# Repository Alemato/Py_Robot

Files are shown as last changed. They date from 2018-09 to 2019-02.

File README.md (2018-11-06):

# Py Robot Project
## Descrizione 
Il Problema "Z" che il rover dovrà risolvere è il seguente:

Cercare e riconoscere un QR code all'interno di un ambiente circoscritto, nel quale il rover naviga in totale sicurezza evitando gli ostacoli tramite i sensori ultrasuoni e la Pi-Camera.
Una volta travto tale QR Code il Rover accendera il led della OpenMV Camera. 

# Specifice Hardware

## Lista dei componenti da aggiungere al Rover 
### Sono i componenti che vorremmo implementare nel progetto.
###### Componenti già in possesso (durante il progetto)
* 1x OpenMV camera 

###### Componenti compranti durante il progetto
* 1x Microswitch con levetta (il linck a seguire sono 10 pz e li useremo tutti) [(acquistato dal gruppo)](https://www.amazon.it/ROSENICE-Pezzi-Interruttore-Levetta-Micro/dp/B01JRORHGE)
* 1x MakerHawk Lidar Laser Range Modulo Modulo a Singolo Punto Micro Range Pixhawk Compatibile con Cavo  [(acquistato dall'Università)](https://www.amazon.it/MakerHawk-Modulo-Singolo-Pixhawk-Compatibile/dp/B0778B15G7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)
* 1x Multistar LiHV ad alta capacità 5200mAh 3S multi-rotore Lipo pack [(acquistato dall'Università)](https://www.amazon.it/Multistar-LiHV-Capacity-5200mAh-Multi-Rotor/dp/B01BJCZ2G4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)
* 1x Set 2 Lipo Voltage Checker (2S - 8S) [(acquistato dall'Università)](https://www.amazon.it/WOSKY-Battery-Indicator-helicopter-quadcopter/dp/B072J71G72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)
* 1x Turnigy Accucel-6 80W 10A Balancer / Charger LiHV Capace [(acquistato dall'Università)](https://hobbyking.com/it_it/turnigy-accucel-6-80w-10a-balancer-charger-lihv-capable.html)
* 1x Turnigy Temperature Sensor for Battery Charger [(acquistato dall'Università)](https://hobbyking.com/it_it/turnigy-temperature-sensor-for-battery-charger.html)
* 1x Turnigy ignifugo LiPoly Bag Batteria (zip) (200x155x95mm) [(acquistato dall'Università)](https://hobbyking.com/it_it/fire-retardant-lipo-battery-bag-220x155x115mm-with-handle.html)
* 1x Sacco 18x22cm ai polimeri di litio ricarica Confezione [(acquistato dall'Università)](https://hobbyking.com/it_it/lithium-polymer-charge-pack-18x22cm-sack.html)
* 1x Foglio Acrilico 500 x 250 X 4 mm [(acquistato dal gruppo)](https://www.amazon.it/Sintetico-Trasparente-Lastra-500x250-spessore/dp/B00HWRE7SK/) 
* 1x Set 4 cavi TX60 [(acquistato dal gruppo)](https://www.amazon.it/gp/product/B07D71VHFG/)
* 1x Set 5 interruttori 16A 250V [(acquistato dal gruppo)](https://www.amazon.it/gp/product/B00WJLF8OQ/)
* 1x PLA BLU ELETTRICO Ø 1,75 MM 750gr Modello  1PLA60507 [(acquistato dal gruppo)](https://www.filoalfa3d.com/it/filo-175mm/8-pla-blu-elettrico-o-175-mm-8050327033504.html)
* 1x Set 20 viti e dadi 4 X 20 mm  [(acquistato dal gruppo)](https://www.leroymerlin.it/catalogo/bullone-testa-bombata-m4-x-20-mm-34445565-p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)
* 1x Set 6 viti e dadi 6 X 50 mm [(acquistato dal gruppo)](https://www.leroymerlin.it/catalogo/bullone-testa-bombata-m6-x-50-mm-34445726-p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)
* 1x Set 20 dadi 6 mm [(acquistato dal gruppo)](https://www.leroymerlin.it/catalogo/dado-autobloccante--m6-35746193-p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)
* 1x Set 30 viti e dadi [(acquistato dal gruppo)](https://www.weldom.fr/weldom/boulon-6-pans-6-8-3x10-acier-zingue-sac-30-1093856.html)

# Specifiche Software

### Specifiche richieste del Professore 
* Cambiare OS da Raspbian a [Ubuntu-Mate 16.04.2](https://ubuntu-mate.org/raspberry-pi)
* Implementare [Ros Kinetic](http://wiki.ros.org/kinetic) come Publish-Subscribe al posto MQTT 
* Implementare IA in Prolog
* Implementare Pi-camera e algoritmo per la rilevazione degli ostacoli
* Implementare voltometro

### Specifiche Aggiuntuve
* Modifica degli sketch degli arduini, standardizzazione in nodi ROS

## Funzione del Microswitch con levetta
Data la scarsa precisone nel rilevare gli ostacoli sottili, ad esempio un piede della sedia, da parte dei tre sensori ad ultrasuoni, i Microswitch con levetta risolveranno tale problema funzionando come un Bumper Sensor.  

## Lista Cartelle e descrizione contenuto

>
py_robot: cartella pricipale che contiene tutto il progetto del rover fisico
>
py_robot_v_rep: cartella che contiene tutto il progetto in versione v-rep
>

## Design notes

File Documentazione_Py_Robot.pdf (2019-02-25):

# DOCUMENTAZIONE PY_ROBOT

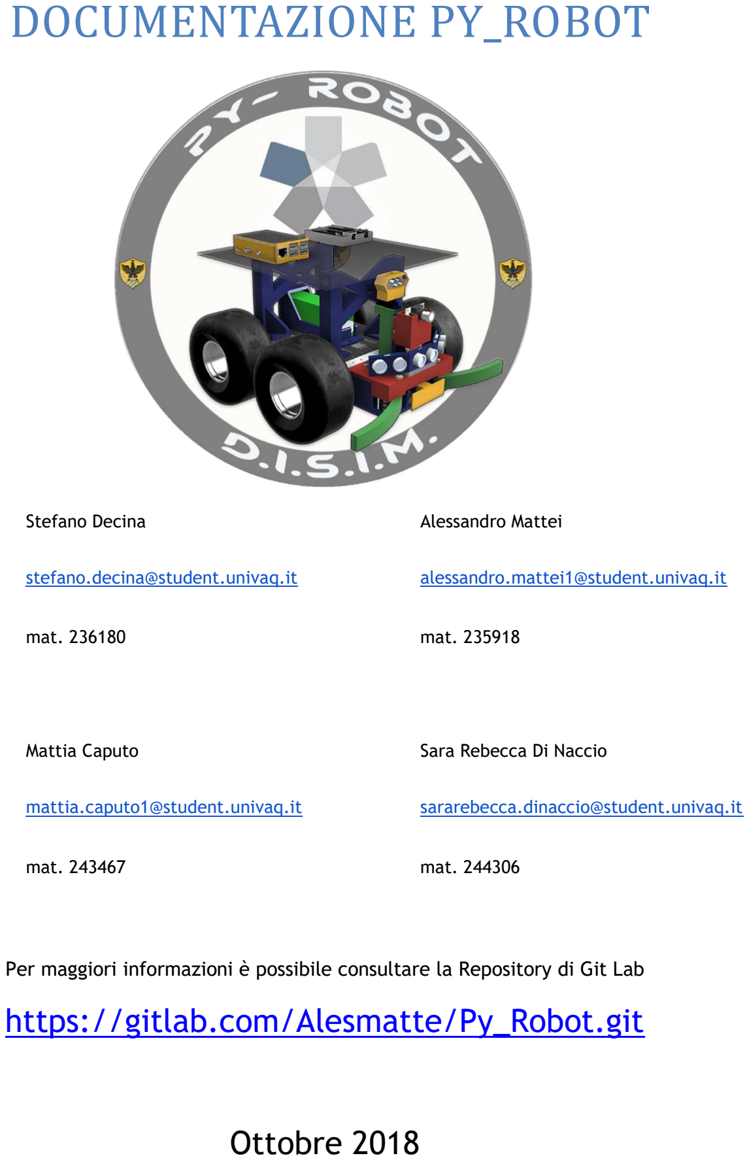
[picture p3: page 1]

Stefano Decina | Alessandro Mattei
stefano.decina@student.univaq.it | alessandro.mattei1@student.univaq.it
mat. 236180 | mat. 235918
Mattia Caputo | Sara Rebecca Di Naccio
mattia.caputo1@student.univaq.it | sararebecca.dinaccio@student.univaq.it
mat. 243467 | mat. 244306

Per maggiori informazioni è possibile consultare la Repository di Git Lab

# https://gitlab.com/Alesmatte/Py_Robot.git

# Ottobre 2018

# SOMMARIO

Sommario | 2
Introduzione | 6
Ruoli dei membri del Team: | 6
Requisiti Funzionali | 7
Componenti del Rover | 7
Telaio del rover | 8
Motori | 8
Ruote | 9
Motor Driver L298N | 10
Pins L298N Motor Driver | 11
Batteria | 13
Sensore Sonar | 16
Pin hc-sr04 | 16
Principio base di funzionamento: | 17
Compass CMP11 | 17
Frequenza di aggiornamento di dati | 18
Selezione della modalità | 18
Comandi Seriali | 19
Calibrazione del CMPS11 | 21
Calibrazione di CMPS11 per funzionamento solo orizontale | 21
Ripristono della calibrazione di fabbrica del CMPS11 | 22
Modifica della velocità di trasmissione | 22
OpenMV Cam M4 V2 | 22
Dimensioni | 23
Pi Camera | 24
Voltometer | 24
Specifiche | 24
Raspberry Pi 3 model B | 25

Accesso alla Raspberry pi 3 | 25
Arduino UNO R3 | 27
Arduino Nano V3.2 | 29
Disegni e Stampe 3D | 30
Baffi | 30
Corpo Frontale | 30
Torri | 31
Case Batteria | 31
Scatola per Alimentazione | 31
Supporto Sonar | 32
Supporto Principale | 32
Connessioni | 33
Arduino Uno – Sonar e Voltmeter | 33
Left Sonar | 33
Right Sonar | 33
Front Sonar | 34
Schema di connessione | 34
Arduino UNO - Compass | 35
Compass | 35
Schema di connessione: | 35
Arduino Nano – Motor Driver e Switch | 36
Motor Driver Sinistro | 36
Motor Driver Destro | 36
Switch 1 | 37
Switch 2 | 37
Switch 3 | 37
Schema di connessione: | 38
Introduzione a ROS | 39
Sistemi operativi Supportati da Ros | 39
ROS Livello file system | 40

ROS Computation Graph Level | 40
Codice | 42
Nodi | 42
Arduino uno: Compass Node | 42
Arduino Nano: Motor Driver & Switch Node | 44
Arduino Nano: Sonar & Voltometer Node | 49
Controller Node | 51
Open_MV Node | 55
Open_CV Node | 57
Prolog_IA_Node | 58
Node Launcher | 65
Messaggi | 65
Compass Node Message | 66
Controller Node Message | 66
Controller To Motor Node Message | 66
MV Camera Node Message | 66
Motor_Switch Node Message | 66
Pi Camera Node Message | 66
Prolog IA Node Message | 67
Sonar_Volt Node Message | 67
Codici VRep | 67
Nodi | 67
Controller Node | 67
Lidar_Compass Node | 72
Motor_Switch Node | 75
OpenCV Node | 79
Prolog_IA Node | 81
Sonar_Volt Node | 90
Launcher | 92
Messaggi | 92

Controller Node Message | 92
Controller to Lidar Node Message | 93
Controller to Motor Node Message | 93
Lidar Compass Node Message | 93
MV Camera Node Message | 93
Motor Switch Node Message | 93
Pi Camera Node Message | 93
Prolog Ia Node Message | 93
Sonar Volt Node Message | 94
Diagrammi | 94
Class Diagram parte fisica | 94
Class Diagram parte virtuale | 95
Component Diagram | 96
Sequence Diagram | 97
NOTE | 98
lIstino prezzi | 100

# CAPITOLO 1

## INTRODUZIONE

Questo Progetto è l’esame finale del corso “Intelligent System and Robotics Laboratory” del Professore Giovanni De Gasperis.

Lo scopo di questo progetto è quello di aggiornare e aggiungere nuove caratteristiche al rover già sviluppato del precedente anno dal team “SmartExploreX”.

In questa nuova versione è stato ridefinito il problema “Z”:

- Navigare liberamente in un ambiente circoscritto, senza urtare oggetti circostanti a lui, in totale sicurezza.
- Cercare e riconoscere un QR code all'interno di un ambiente circoscritto.
- Una volta trovato tale QR Code il Rover emetterà un suono tramite un Buzzer.

## RUOLI DEI MEMBRI DEL TEAM:

### Stefano Decina:

- Sviluppo Arduino
- Sviluppo Ros
- Modellazione 3D per stampe 3D
- Animazione 3D
- Sviluppo V-rep
- Sviluppo I.A.
- Beta tester

### Alessandro Mattei:

- Specialista Hardware
- Implementazione Raspberry
- Sviluppo Arduino
- Sviluppo Ros
- Sviluppo V-rep
- Sviluppo OpenMV
- Sviluppo OpenCV
- Sviluppo I.A
- Beta Tester

### Mattia Caputo:

- Sviluppo V-rep
- Sviluppo Ros
- Sviluppo OpenCV
- Sviluppo I.A.
- Beta tester
- Presentazione

### Sara Rebecca Di Naccio:

- Sviluppo Arduino
- Sviluppo Ros
- Sviluppo I.A
- Documentazione
- Presentazione
- Beta tester

REQUISITI FUNZIONALI

Il rover deve:

- Navigare liberamente e in sicurezza in un ambiente sconosciuto.
- Riconoscere gli ostacoli tramite pi-camera e sempre tramite essa riconoscere il percorso più sicuro.
- Riconoscere gli ostacoli tramite i sensori a ultrasuoni.
- Riconoscere gli ostacoli tramite il LIDAR.
- Riconoscere un urto con un oggetto tramite i micro-switch
- Fermarsi e cercare una via sicura in caso di urto.
- Riconoscere un QR code tramite OpenVM e fermarsi.
- Evitare gli ostacoli presenti nell’ambiente.
- Aggiustare la direzione tramite la bussola.

# COMPONENTI DEL ROVER

Il rover è composto dai seguenti componenti:

- 1X Telaio del rover, in alluminio.
- 4X Motori spazzolati da 12V 0,37A.
- 4X Ruote da offroad.
- 2X Motor Driver L298N.
- 1X Batteria LiHV 3S 5200mah 10C con uscita 52A (in sostituzione alla batteria li-ion 12v 4500mah con uscita 2A, non in grado di alimentare tutto il sistema).
- 3X Sensori ad ultrasuoni HC-SR04 (due in più rispetto alla versione precedente del rover).
- 1X Micro servo SG90 (non presente nella versione precedente del rover).
- | 1X Analog | voltage divider V2 (Non presente nella versione precedente del rover)
- 1X Compass CMP11 Tilt Compensated Magnetic Compass.
- 1X OpenMv (non presente nella versione precedente del rover).
- 1X Pi-Camera (non presente nella versione precedente del rover).
- 1X Raspberry Pi 3 model B
- 1X Arduino Uno R3
- 2X Arduino Nano V3.2
- 10X Micro Switch a levetta (non presenti nella versione precedente del rover).
- 1X Plexiglass di dimensioni:
- Vari Componenti disegnati e stampati in 3D

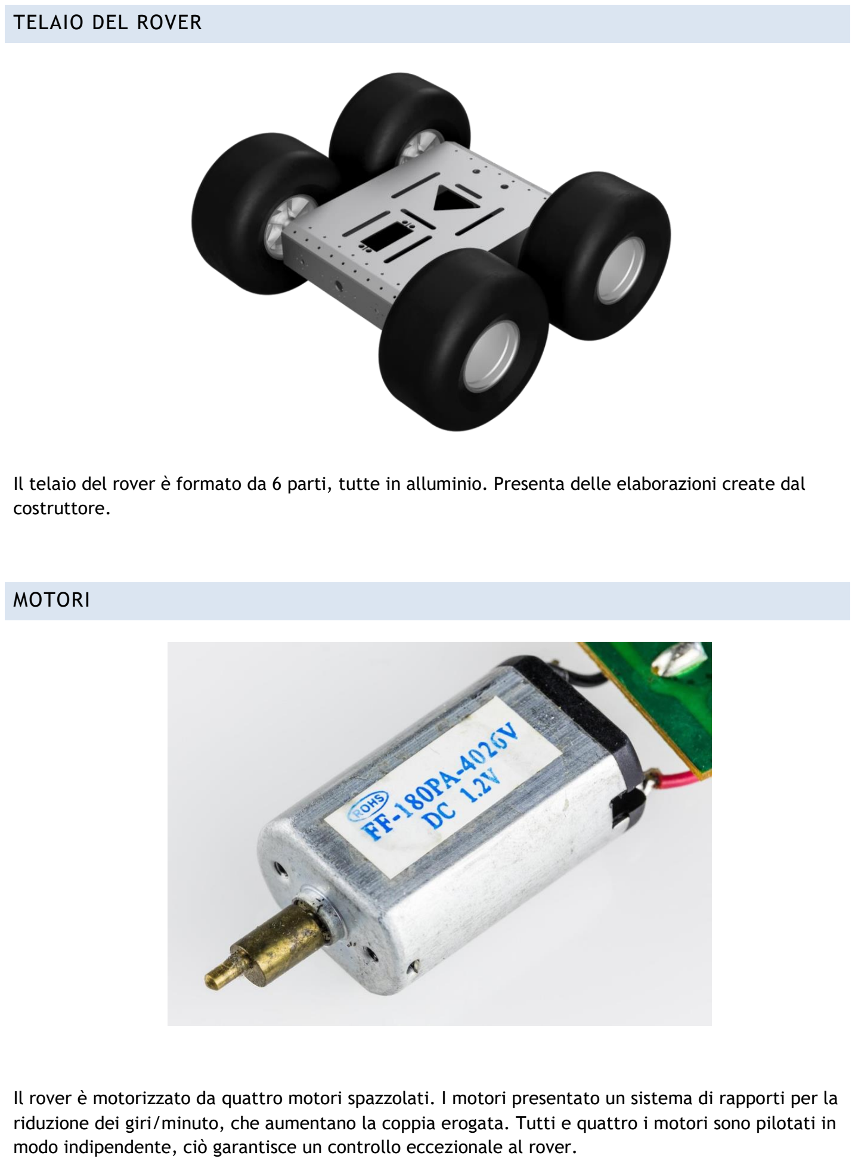
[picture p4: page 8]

TELAIO DEL ROVER

Il telaio del rover è formato da 6 parti, tutte in alluminio. Presenta delle elaborazioni create dal costruttore.

MOTORI

Il rover è motorizzato da quattro motori spazzolati. I motori presentato un sistema di rapporti per la riduzione dei giri/minuto, che aumentano la coppia erogata. Tutti e quattro i motori sono pilotati in modo indipendente, ciò garantisce un controllo eccezionale al rover.

## Specifiche tecniche:

Tipologia di motore: | Spazzolato con riduzione
Tipologia di corrente di funzionamento: | DC
Voltaggio Nominale: | 12V
Amperaggio Nominale: | 0.37A
Rapporto di riduzione: | ND

RUOTE

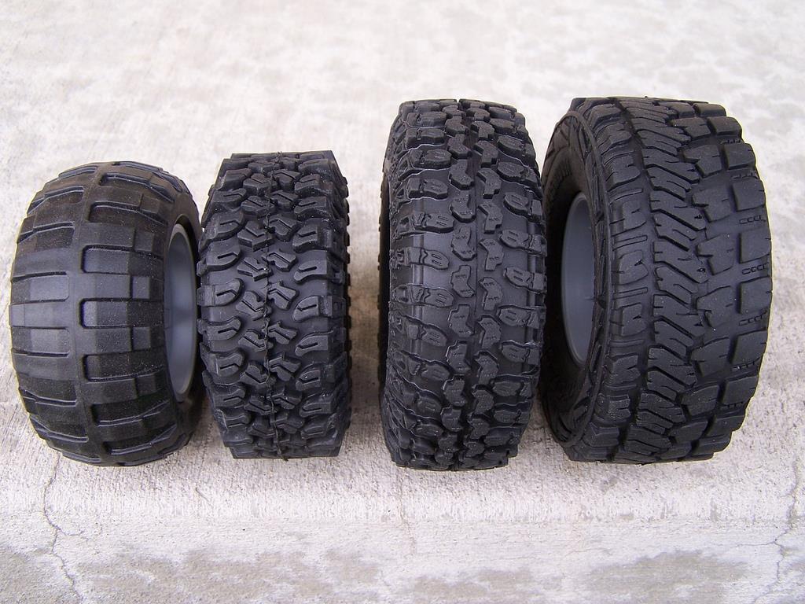
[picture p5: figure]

Il rover è dotato di quattro ruote di tipo off road.

## Specifiche tecniche:

Dimensioni: | ND

MOTOR DRIVER L298N

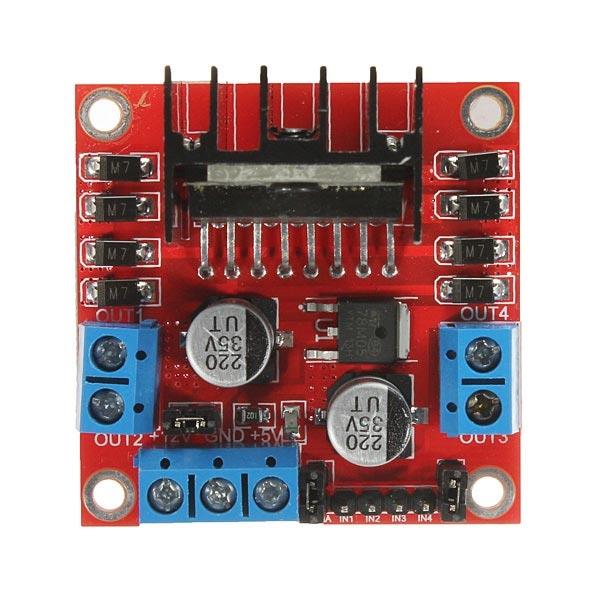
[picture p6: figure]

Il rover è dotato di 2 motor driver L298N.

La funzione dei motor driver è quella di prendere un segnale di controllo a bassa corrente e trasformarlo in un segnale a più alta potenza in grado di pilotare un motore. In questo progetto ne useremo 2 perché ciascun driver può pilotare autonomamente 2 motori.

Un H-Bridge è un circuito in grado di pilotare una corrente in entrambe le polarità ed essere controllato dalla Pulse Width Modulation (PWM). Una modulazione a larghezza di impulso (PWM) è una tecnica di modulazione utilizzata per codificare un messaggio in un segnale pulsante. Sebbene questa tecnica di modulazione possa essere utilizzata per codificare le informazioni per la trasmissione, il suo uso principale è quello di consentire il controllo della potenza fornita ai dispositivi elettrici, in particolare ai carichi inerziali come i motori. Più gli impulsi sono lunghi più la ruota si gira più velocemente, più gli impulsi sono brevi, più lentamente ruota la ruota idraulica. I motori dureranno molto più a lungo e saranno più affidabili se controllati tramite PWM

## Specifiche tecniche:

- | Tensione di alimentazione: | VM = 35V (max.)
- | Corrente di uscita Iout: | 2 A (picco)
- | Modalità di funzionamento: | CW / CCW / freno corto / arresto

PINS L298N MOTOR DRIVER

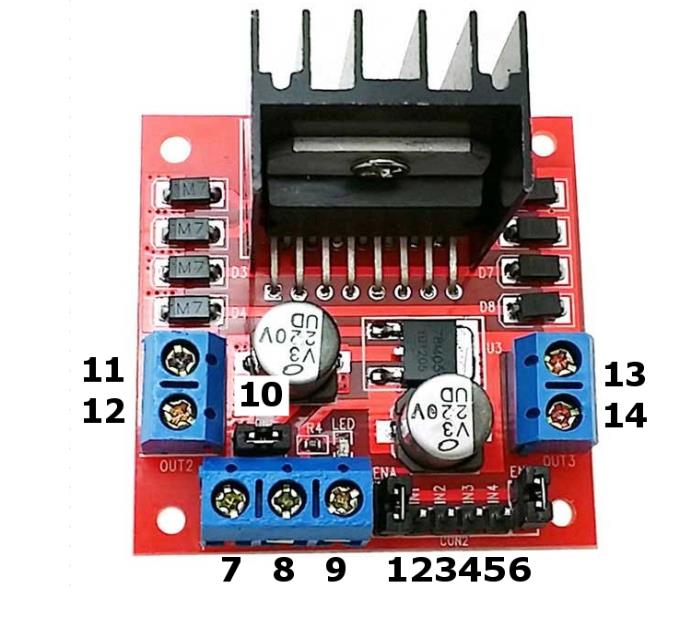
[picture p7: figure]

N° | DESCRIZIONE
1 | ENA - ponticello di abilitazione motore a corrente continua A Non rimuovere nel caso si utilizzi un motore passo-passo. Connettersi a un'uscita PWM per il controllo della velocità del motore DC.
2 | IN 1
3 | IN 2
4 | IN 3
5 | IN 4
6 | ENB - ponticello di abilitazione motore a corrente continua B Non rimuovere nel caso si utilizzi un motore passo-passo. Connettersi a un'uscita PWM per il controllo della velocità del motore DC.

7 | Collegare la tensione di alimentazione del motore, massima di 35V DC. Rimuovere il ponticello [10] se la tensione è > 12V DC
8 | GND
9 | uscita 5V se 12V ponticello in luogo, ideale per alimentare il vostro Arduino (etc)
10 | jumper 12V - rimuovere questo se si utilizza una tensione di alimentazione superiore a 12V DC. Ciò consente l'alimentazione tramite il regolatore 5V di bordo
11 | DC motor 1 "+" o motore passo-passo A +
12 | motore DC 1 "-" o motore passo-passo A-
13 | motore a corrente continua 2 "+" o motore passo-passo B +
14 | motore DC 2 "-" o motore passo-passo B-

BATTERIA

Il rover nella precedente versione era dotato di una batteria Li-ion con uscita di 1A che non era in grado di alimentare tutto il sistema, abbiamo quindi dovuto sostituire la batteria con una più potente una Lipoly LiHV.

Le batterie Lipoly ad alta tensione (LiHV) offrono una maggiore densità di potenza rispetto alle tradizionali batterie lipo che consentono di aumentare i tempi di utilizzo senza la penalità di peso aggiuntivo.

LiHV sta per "High Voltage Lithium Polymer”. I vantaggi delle batterie LiHV sono la maggiore potenza e tempi di funzionamento più lunghi. Le batterie LiHV possono essere caricate a 4,35 V per cella, superiori alle normali batterie LiPo che si trovano a 4,20 V. Ad esempio, un pacco LiHV 3S caricato a 4,35 V darebbe 13,05 V. Considerando che una batteria Lipo con la stessa carica otterrebbe solo 12,6V. Le batterie LiHV hanno anche una resistenza interna inferiore.

Il grosso svantaggio risiede nella pericolosità delle batterie stesse.

La batteria può esplodere se corto-circuitata, a causa della bassissima resistenza interna e della conseguente tremenda corrente impulsiva che attraversa la cella. Inoltre, una cella Li-Poly può incendiarsi facilmente se forata, per cui le batterie sono, in varie applicazioni, ricoperte da un involucro plastico che dovrebbe prevenire le forature.

Queste batterie necessitano di usare caricabatterie specifici (vedi foto), per evitare, appunto, incendi ed esplosioni.

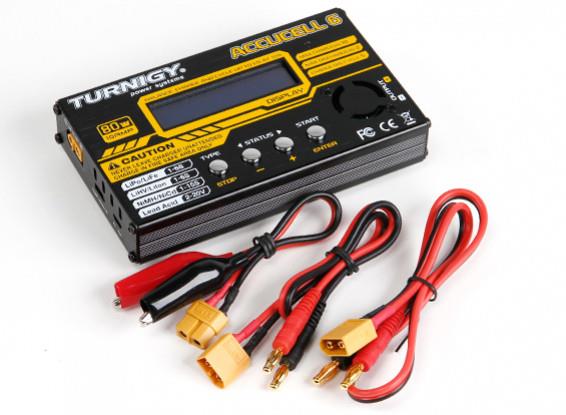
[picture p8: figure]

## Specifiche tecniche Batteria:

Capacità Minima: | 5200mAh
Configurazione: | 3S / 11.4v / 3Cell

Costante di Scaricamento Nominale: | 10C
Constante di Scaricamento Picco (10sec): | 20C
Peso Batteria: | 318g
Dimensioni: | 108 x 36 x 47 mm
Charge Plug: | JST-XH
Discharge Plug: | XT60

SENSORE SONAR

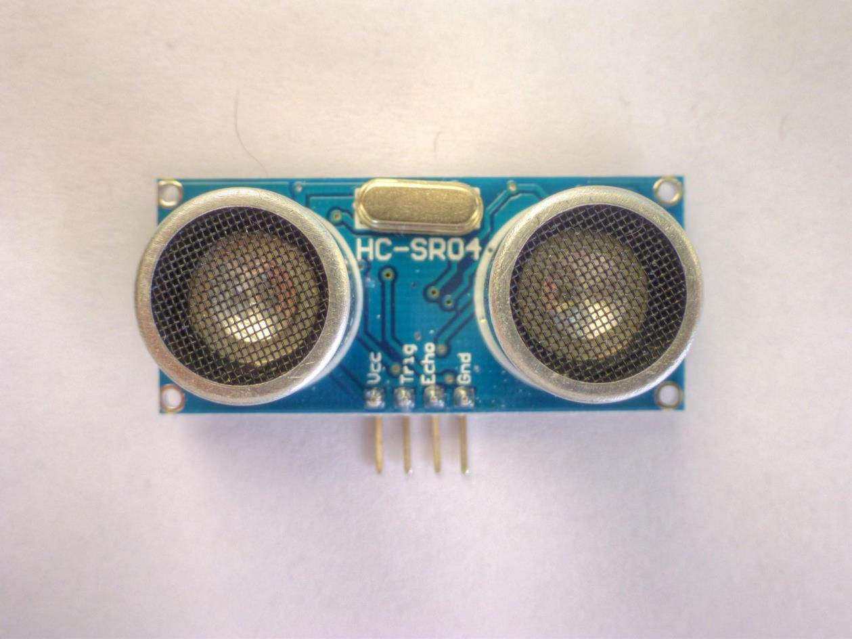
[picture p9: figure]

Il rover è provvisto di 3 sensori sonar di tipo HC-SR04, questo sensore ha un trasmettitore, che invia onde ultrasoniche e un ricevitore, che prende il segnale. Si basa sulla tecnologia Sonar sound navigation and ranging, è una tecnica che utilizza la propagazione del suono per la navigazione e per rilevare la presenza e la posizione di oggetti nello spazio.

## Specifiche tecniche:

- Tensione di alimentazione: | 5V DC
- Corrente di alimentazione: | 15mA
- Frequenza di funzionamento: | 40Hz
- Segnale input Trigger: | 10uS TTL per impulso
- Angolo di funzionamento: | 15 gradi
- Raggio misurato: | 2cm - 400cm

PIN HC-SR04

- Vcc: 5VDC

- Trig: Trigger pin
- Echo: Echo pin
- GND: ground

PRINCIPIO BASE DI FUNZIONAMENTO:

Utilizzo dell’IO trigger per almeno 10 microsecondi di segnale in HIGH.

Il modulo invierà automaticamente 8 cicli di impulsi a 40 khz per aumentare eco e rileverà se è presente un segnale di impulso.

Per calcolare la distanza tra il sensore e l’oggetto si misura l’intervallo di tempo tra il trigger e eco.

Le formule per calcolare la distanza è “intervallo di tempo / 58” per le misure in centimetri oppure “intervallo di tempo / 148” per i pollici. In alternativa a queste due formule abbiamo: “Intervallo = tempo di livel HIGH * velocità del suono (340 m/s) /2”.

Nota bene: se l'angolo di impatto del segnale con l'ostacolo è superiore a 15 gradi, nessun segnale sarà restituito. Inoltre, se c'è un ostacolo vicino al sensore (2 cm o meno), ci possono essere alcuni problemi nelle letture.

COMPASS CMP11

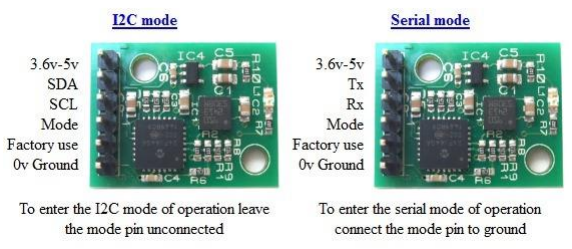
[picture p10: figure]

Il modulo CMPS11 è una vera bussola con tilt, compensazione dell'inclinazione. A differenza dei moduli simili che forniscono solo i dati grezzi, questa piccola scheda incorpora un potente processore a 16 bit che esegue tutti i calcoli complessi per fornire un'uscita da 0 a 359,9 gradi.

Il CMP11 implementa un magnetometro a 3 assi, un giroscopio a 3 assi e un accelerometro a 3 assi. Un filtro Kalman viene applicato al giroscopio e l'accelerometro per rimuovere gli errori causati dall'inclinazione del PCB.

Il CMPS11 produce un risultato di 0-3599 che rappresenta 0-359,9 o da 0 a 255 gradi. L'uscita dei tre sensori che misurano le componenti x, y e z del campo magnetico, insieme con il beccheggio e il rotolo, vengono utilizzati per calcolare il bearing, ciascuno di questi componenti sono resi disponibili anche in forma grezza. Il modulo CMPS11 richiede un'alimentazione a 3,6-5 V e assorbe una corrente nominale di 25 mA. Viene fornita una scelta di interfacce Seriale o I2C.

Questa bussola ritorna le seguenti misure:

- Angolo 8-Bit
- Angolo 16-Bit
- Accellerometro
- Temperatura
- Giroscopio
- Angolo Beccheggio
- Angolo Imbardata
- Angolo Rollio

## Tecniche:

- | Uscita Compens Compensated Tilt: | da 0 a 359.0 gradi
- | Tensione di alimentazione: | da 3,6 V a 5 V
- | Corrente: | 35 mA tip.
- | Risoluzione: | 0,1 gradi
- | Precisione: | migliore del 2% dopo la calibrazione
- | Livelli di segnale: | 3,3 V, 5 V tollerante
- | Modalità I2C: | fino a 100 kHz
- | Modalità seriale: | 9600, 19200, 38400 baud

FREQUENZA DI AGGIORNAMENTO DI DATI

Gli aggiornamenti dell'intestazione compensata di inclinazione si verificano a 75hz con i dati filtrati per mezzo di un buffer di 45 campioni, ciò significa che viene eseguito un aggiornamento completo del buffer ogni 640ms. I dati grezzi del magnetometro e dell'accelerometro sono disponibili ogni 13,3ms.

SELEZIONE DELLA MODALITÀ

CMPS11 esamina solo i pin di selezione della modalità all'accensione.

Per entrare nella modalità operativa I2C lasciare il pin della modalità non connesso

Per accedere alla modalità operativa seriale collegare il pin della modalità a terra

### Comunicazione seriale:

Per il rover abbiamo optato per la comunicazione seriale, perché è più compatibile con l'utilizzo che ne facciamo. La modalità seriale opera su un collegamento con una velocità di trasmissione predefinita di 9600 bps (senza parità, 2 bit di stop) e livelli di segnale 3.3v-5v.

COMANDI SERIALI

Di seguito una tabella che descrive i comandi che possono essere inviati a CMPS11 e i dati con cui risponderà.

Comando | Nome | I byte restituiti | Descrizione dei dati restituiti
0x11 | OTTIENI LA VERSIONE | 1 | Versione software
0x12 | OTTENERE UN ANGOLO DI 8 BIT | 1 | Angolo come singolo byte 0-255
0x13 | OTTENERE UN ANGOLO DI 16 BIT | 2 | Angolo come due byte, byte alto prima 0-3599
0x14 | Ottieni PITCH | 1 | Angolo di inclinazione +/- 0-85 ° Kalman filtrato
0x15 | RICEVI | 1 | Angolo di rollio +/- 0-85 ° Kalman filtrato

0x16 | OTTIENI PITCH NO KAL | 1 | Angolo di inclinazione +/- 0-85 ° senza filtro Kalman
0x17 | ROLL NO NO KAL | 1 | Angolo di rollio +/- 0-85 ° senza filtro Kalman
0x19 | OTTIENI MAG RAW | 6 | Dati magnetici grezzi, firmati a 16 bit: X alto, X basso, Y alto, Y basso, Z alto, Z basso
0x20 | OTTIENI ACCEL RAW | 6 | Dati di accelerometro grezzi, firmati a 16 bit: X alto, X basso, Y alto, Y basso, Z alto, Z basso
0x21 | OTTIENI GYRO RAW | 6 | Dati gyro grezzi, firmati a 16 bit: X alto, X basso, Y alto, Y basso, Z alto, Z basso
0x22 | OTTIENI TEMP | 2 | Temperatura come due byte, byte alto prima 0. Risoluzione tipica 8 LSB / ° C
0x23 | PRENDI TUTTO | 4 | angolo alto, angolo basso (0-3599), altezza (+/- 0-85), rotazione (+/- 0-85)
0xF0 | CALIBRAZIONE BYTE 1 | 1 | restituisce ok (0x55)
0xF5 | CALIBRAZIONE BYTE 2 | 1 | restituisce ok (0x55)
0xF6 | CALIBRAZIONE BYTE 3 PIENO | 1 | restituisce ok (0x55)
0xF7 | CALIBRAZIONE BYTE 3 FLAT | 1 | restituisce ok (0x55)
0xF8 | USCITA CALIBRAZIONE | 1 | restituisce ok (0x55)
0x6A | RIPRISTINO 1 | 1 | restituisce ok (0x55)
0x7C | RIPRISTINO 2 | 1 | restituisce ok (0x55)
0x81 | RIPRISTINO 3 | 1 | restituisce ok (0x55)

0xA0 | BAUD 19200 | 1 | restituisce ok (0x55)
0xA1 | BAUD 38400 | 1 | restituisce ok (0x55)

CALIBRAZIONE DEL CMPS11

Si prega di non farlo finché la comunicazione seriale non funziona completamente. Consiglierei di valutare le prestazioni del CMPS11 prima di implementare questa funzione.

Il suo scopo è quello di rimuovere il guadagno del sensore e l'offset sia del magnetometro che dell'accelerometro e ottiene ciò cercando le massime uscite del sensore. Prima di tutto è necessario accedere alla modalità di calibrazione inviando una sequenza di 3 byte di 0xF0,0xF5 e quindi 0xF6 (leggendo il byte di conferma dopo ognuno di essi).

Il LED si spegnerà e il CMPS11 dovrebbe ora essere ruotato in tutte le direzioni in 3 dimensioni, se viene rilevato un nuovo massimo per uno qualsiasi dei sensori, il LED lampeggerà, quando non è possibile ottenere altri LED lampeggianti in qualsiasi direzione, quindi uscire dalla modalità di calibrazione con un comando di 0xF8.

Accertarsi che CMPS11 non si trovi vicino a oggetti ferrosi in quanto ciò potrebbe distorcere il campo magnetico e causare errori nella lettura. Durante la calibrazione ruotare lentamente la bussola.

Ricorda che l'asse del campo magnetico è improbabile che sia orizzontale, si immerge nella terra con un angolo che varia a seconda della posizione. Nei nostri uffici nel Regno Unito si immerge nella terra a 67 gradi e questo è l'orientamento che ogni asse della bussola deve essere per trovare i massimi.

È necessario trovare sia i massimi positivi che quelli negativi per ciascun asse, quindi ci sono 6 punti da calibrare. Anche l'accelerometro è calibrato allo stesso tempo, pertanto il modulo deve essere posizionato orizzontalmente, invertito e su tutti e 4 i lati per calibrare i 6 punti dell'accelerometro.

Ogni punto dell'accelerometro deve essere stabile per 200 mS per la sua lettura da utilizzare per la calibrazione.

Questo ritardo è intenzionale in modo che i leggeri colpetti al modulo non producano letture accelerometriche che compromettono gli angoli di beccheggio e rollio.

Non c'è ritardo per i punti magnetici. Le prestazioni del modulo sono direttamente correlate a quanto bene si esegue la calibrazione, quindi farlo lentamente e con attenzione.

CALIBRAZIONE DI CMPS11 PER FUNZIONAMENTO SOLO ORIZONTALE

Se la bussola non richiede la compensazione dell'inclinazione, può essere utilizzata una semplice calibrazione che può essere implementata solo con una rotazione sul piano orizzontale.

Prima di tutto è necessario accedere alla modalità di calibrazione inviando una sequenza di 3 byte di 0xF0,0xF5 e quindi 0xF7 (leggendo il byte di conferma dopo ognuno di essi).

Il LED si spegnerà e il CMPS11 dovrebbe ora essere ruotato in tutte le direzioni su un piano orizzontale, se viene rilevato un nuovo massimo per uno qualsiasi dei sensori, il LED lampeggerà, quando non è possibile ottenere altri LED lampeggianti in qualsiasi direzione, quindi uscire la modalità di calibrazione con un comando di 0xF8.

Accertarsi che CMPS11 non si trovi vicino a oggetti ferrosi in quanto ciò potrebbe distorcere il campo magnetico e causare errori nella lettura. Durante la calibrazione ruotare lentamente la bussola.

RIPRISTONO DELLA CALIBRAZIONE DI FABBRICA DEL CMPS11

Per eseguire un ripristino della calibrazione di fabbrica, scrivere una sequenza di 3 comandi nell'ordine corretto. La sequenza è 0x6A, 0x7C, 0x81 (leggendo il byte di conferma dopo ognuno di essi).

MODIFICA DELLA VELOCITÀ DI TRASMISSIONE

La velocità di trasmissione seriale predefinita di 9600 può essere modificata. Ci sono altre due velocità di trasmissione che possono essere utilizzate, per il 19200 basta inviare 0xA0 o in alternativa per 38400 inviare 0xA1.

Si noti che CMPS11 sarà sempre impostato sulla frequenza 9600 bps dopo il ciclo di accensione e dopo aver impostato una nuova velocità di trasmissione, la risposta ok (0x55) verrà inviata alla velocità appena selezionata.

OPENMV CAM M4 V2

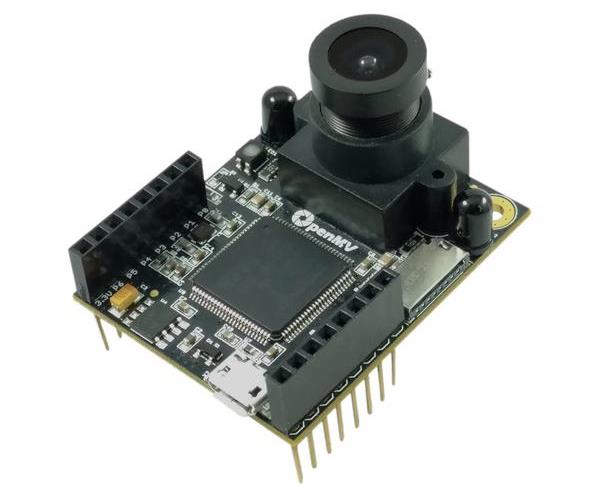
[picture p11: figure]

OpenMV Cam è una piccola scheda a microcontrollore a bassa potenza che consente di implementare facilmente le applicazioni utilizzando la visione artificiale nel mondo reale.

La OpenMV Cam si programma con script Python di alto livello, ciò rende più facile gestire i complessi output degli algoritmi di visione artificiale e lavorare con strutture di dati di alto livello.

DIMENSIONI

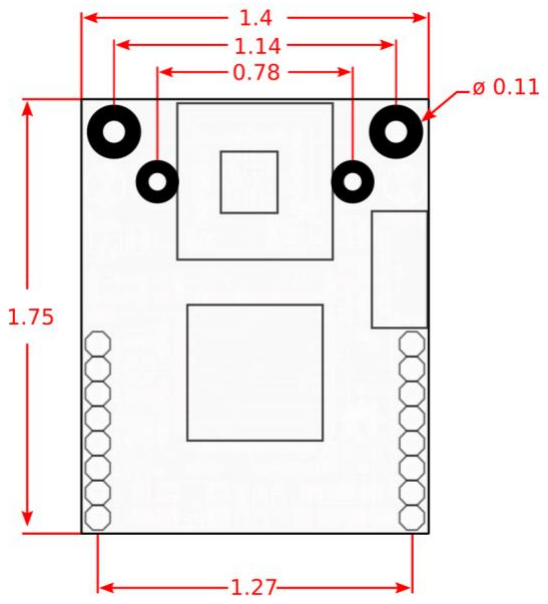
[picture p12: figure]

## Specifiche tecniche:

- Processore: CPU ARM® a 32 bit Cortex®-M4 con FPU a singola precisione 180 MHz (225 DMIPS). Punteggio Mark Mark: 608 (confronta con Raspberry Pi Zero: 2060)
- | Memoria RAM: | 64 KB .DATA /. BSS / Heap / Stack 192KB Frame Buffer / Stack (256 KB
totali)
- Memoria Flash: Firmware da 9KBK Firmware da 9KB per bootloader 48KB 16KB (1MB totale)
- Formati Immagine: JPEG in scala di grigi RGB565
- Risoluzioni supportate: Scala di grigi: 320x240 e minore RGB565: 320x240 e inferiore. Scala di grigi JPEG: 320x240 e minore RGB565 JPEG: 320x240 e minore
- Lente: Lunghezza focale: 2,8 mm Apertura: F2.0 Formato: 1/3 " HFOV = 70,8 °, VFOV = 55,6 °Mount: M12 * 0,5 Filtro IR tagliato: 650nm (rimovibile)
- | Informazioni elettriche: | Tutti i pin hanno un output di 3,3V re tollerano fino a 5V.
Tutti i pin possono | erogare fino a 25 mA. Ilpin P6 non ha tolleranza 5V in modalità ADC
o DAC. In | totale tutti i pin erogano fino a 120 mA .
- Peso: 16g
- Dimensioni: 45mm x 36mm x 30mm
- | Consumo: Idle 100mA @ 3.3V | Attivo 150mA @ 3.3

PI CAMERA

Il rover è dotato del modulo ottico Pi-Camera per Raspberry-Pi 3 B, verrà usato per identificare visivamente gli ostacoli che si presentano dinanzi al rover.

VOLTOMETER

L’analog voltage divider V2 può rilevare la tensione di alimentazione da 0,0245 V a 25 V. Questo modulo è basato sul principio del divisore del resistore. Il modulo di rilevamento della tensione consente di ridurre la tensione di ingresso 5 volte. Poiché la tensione di ingresso analogico di Arduino è normalmente massima di 5 V, la tensione di ingresso del modulo di rilevamento della tensione analogica non può superare 5 Vx5, ovvero 25 V.

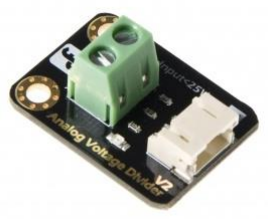
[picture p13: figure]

SPECIFICHE

- Interface: Analog
- Input Voltage (DC): Massimo 25V, Minimo 0.0245V
- Rivela la tensione di alimentazione fino a 25 V
- Size: 22x30mm (0.87 x 1.18 in)

RASPBERRY PI 3 MODEL B

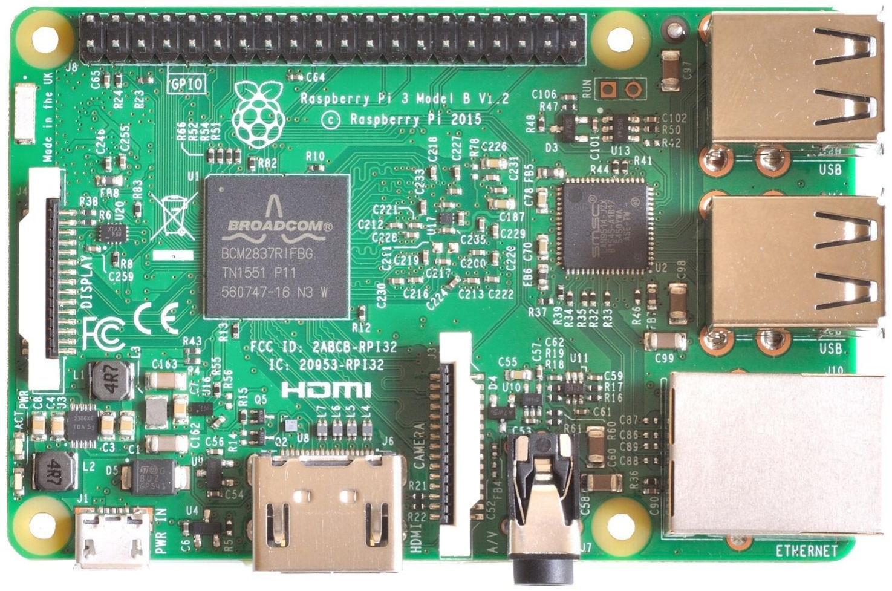
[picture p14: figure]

Il rover utilizza come Main Logic Board la Raspberry Pi model 3 B. È un Singol-Broad Computer di cui è dotato di un processore ARM e una GPU VideoCore. È stato scelto di installare il Sistema operativo Ubuntu MATE in quanto compatibile con la tecnologia ROS Kinetic.

ACCESSO ALLA RASPBERRY PI 3

Possiamo entrare nella raspberry attraverso la connessione wi fi o la connessione ethernet. Entrambi usano il protocollo SSH.

### Connessione Ethernet:

- Windows - collegare il cavo Ethernet nei dispositivi. Dopodiché condividere la connessione con il laptop. Ora, utilizzare un programma come Putty per stabilire una connessione SSH. Se non si conosce ip del raspberry pi basterà digitare a posto del ip il seguente dominio raspberrypi.local.
- Linux e Mac - Devi conoscere l'indirizzo IP di Raspberry Pi, come sopra se non conosci l’indirizzo puoi accedere tramite il dominio Raspberrypi.local.
Per accedere al tuo Raspberry Pi, apri un Terminale e digita il seguente comando:
ssh -XC pi@<indirizzo ip>. Ricorda che pi è il nome utente del Raspberry Pi. Con l’opzione -XC si mette a disposizione X11 Forwording, e sarà possibile riprodurre intero Desktop Enviroment del Raspberry Pi.

### Connessione WIFI:

Per stabilire una connessione WiFi, basterà accedere alla rete wi-fi creata dal raspberry pi con la seguente Password: raspberrypi

### Specifiche tecniche:

SoC | Broadcom DCM2837
CPU | 1.2 GHz 64-bit quad-core ARM Cortex A
GPU | Broadcom VideoCore IV, OpenGL ES 2.0, 1080p30 H.264 high-profile decoder ed encoder 250 MHz per BCM2835 e BMC2836. 400 MHz dual core per BMC2837 (1080p60)
MEMORIA (SDRAM) | 1 GB (condivisa con la GPU) LPDDR2
PORTE USB | 2.0 X4 (attraverso un hub USB integrato)
INPUT | Video Connettore 15-pin MIPI Camera Interface (CSI), utilizzabile con fotocamere Raspberry Pi o Raspberry Pi NoIR
Output Video | Un connettore RCA per il video ed una porta HDMI
Input audio | Attraverso l’interfaccia bus seriale I²S
Output audio | Jack da 3,5 mm, HDMI, attraverso attraverso l’interfaccia bus seriale I²S
Memoria | MicroSD
Collegamenti di rete | Ethernet 10/100 mb/s, wireless LAN 802.11n, Bluetooth 4.1
Connettori di I/O | X40 GPIO
Orologio | Nessun orologio RTC a bordo
Corrente | 800 mA (4,0 W) assorbita
Alimentazione | 5 V via MicroUSB o GPIO
Dimensioni | PCB: [(85,60 mm x 53,98 mm) (3,370079-inch x 2,1251969 inch)] Tot: [(85,60 mm x 56 mm) (3,370079 inch x 2,20472 inch)]

ARDUINO UNO R3

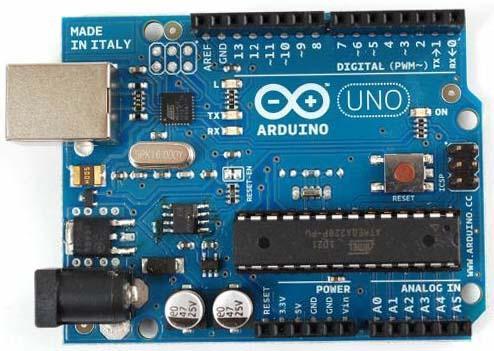
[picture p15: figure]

Arduino Uno è un dispositivo basato su microcontrollore che permette di realizzare diversi tipi di circuiti elettronici. Possiede 14 pin digitali programmabili come ingressi o uscite (i quali hanno anche la capacità di essere utilizzati per funzioni dedicate come la generazione di segnale PWM o la comunicazione UART) e 6 ingressi per l’acquisizione ed elaborazione di segnali analogici. Il microcontrollore è l’ATmega328 prodotto da Atmel, ha una velocità di 16MHz, una memoria flash da 32KB, una ram da 2KB e una memoria EEPROM da 1KB. L’alimentazione della scheda avviene tramite porta usb o tramite l’apposito connettore. In caso siano collegati sia il cavo usb sia il connettore di alimentazione, la scheda è capace di scegliere automaticamente la fonte di alimentazione esterna.

La connessione USB ha 2 funzioni:

- Fornire il circuito
- Permettere lo scambio di dati tra Arduino e altri dispositivi.

## Specifiche tecniche:

Tipo Microcontrollore | Atmel ATmega328
Tensione di lavoro | 5Vdc
Tensione di alimentazione consigliata | da 7Vdc a 12Vdc
Pin digitali | 14 configurabili come ingressi o uscite
Pin analogici | 6 ingressi
Massima corrente per pin digitale | 40mA massima
Memoria Flash | 32KB
Memoria Sram | 2KB
Memoria EEPROM | 1KB
Velocità di clock del microcontrollore | 16MHz

ARDUINO NANO V3.2

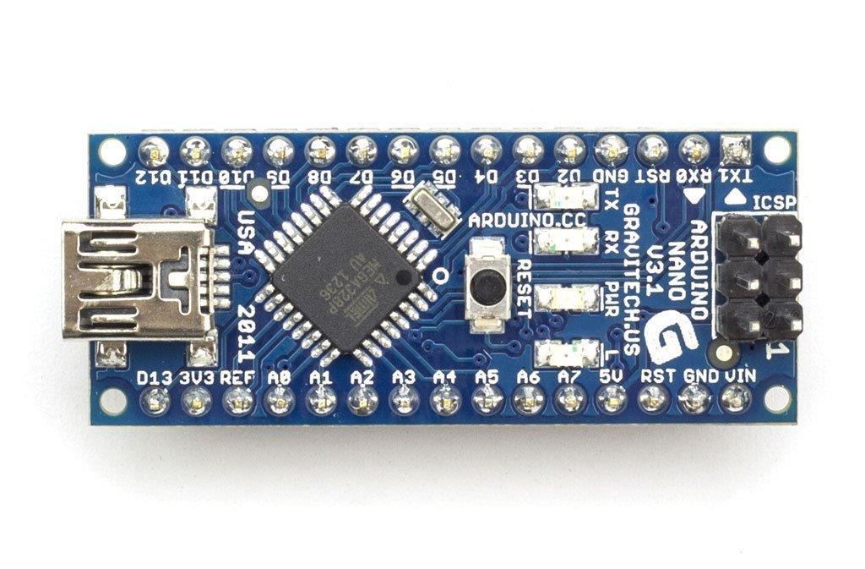
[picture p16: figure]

Arduino Uno è un dispositivo basato su microcontrollore che permette di realizzare diversi tipi di circuiti elettronici. Possiede 14 pin digitali programmabili come ingressi o uscite (i quali hanno anche la capacità di essere utilizzati per funzioni dedicate come la generazione di segnale PWM) e 8
ingressi per l’acquisizione ed elaborazione di segnali analogici e un oscillatore a 16 MHz. | Utilizza un
processore ATMEGA328 che ha 32 kB di memoria per il programma. Manca di un jack di alimentazione e viene programmata attraverso un cavo USB mini.

Specifiche Tecniche:

- Microcontrollore: | ATmega328
- Tensione operativa: | 5 V
- Tensione di ingresso: | da 7 a 12 V
- I/O digitali: | 14 (di cui 6 utilizzate come uscite PWM)
- Ingressi analogici: | 8
- Corrente DC per pin I/O: | 40 mA
- Memoria Flash: | 32 kB (di cui 2 kB utilizzati dal bootloader)
- SRAM: | 2 kB
- EEPROM: | 1 kB
- Clock: | 16 MHz
- Dimensioni (mm): | 45x18x18

# DISEGNI E STAMPE 3D

BAFFI

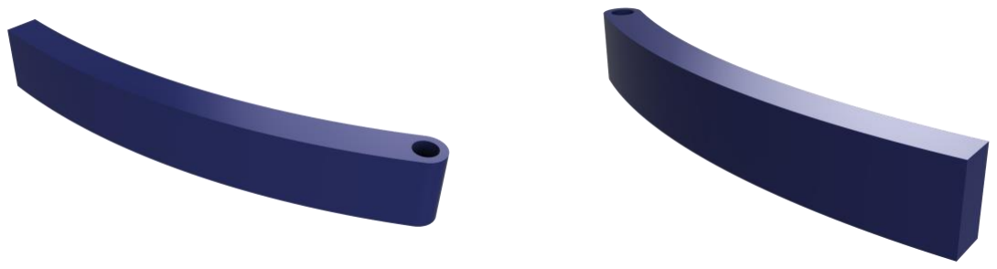
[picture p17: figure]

BAFFO DESTRO | BAFFO SINISTRO

Questi due oggetti vengono posti come due baffi nella zona anteriore del Rover. Hanno la capacità di attivare i microswitch quando il Robot colpirà un oggetto X lateralmente (ossia o a destra o a sinistra, ma sempre davanti). In seguito, i microswitch saranno in grado di far tornare il baffo al suo posto e così che la simulazione può procedere.

CORPO FRONTALE

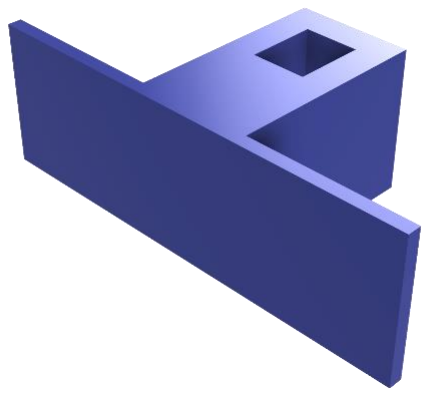
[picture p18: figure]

Ha la stessa funzionalità dei “Baffi”, quello di far attivare i microswitch nel momento dell’impatto ma con l’unica differenza che il Rover rileverà l’ostacolo esattamente nella parte centrale della zona anteriore affinché la sua funzione abbia effetto.

TORRI

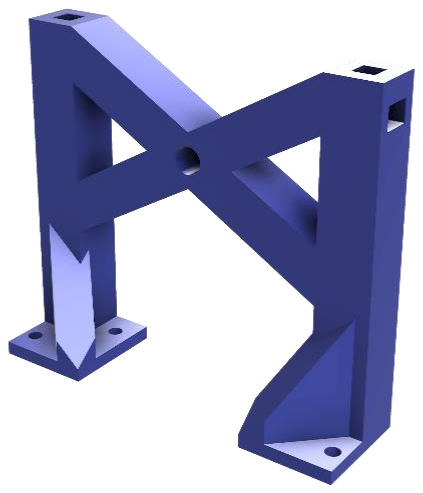
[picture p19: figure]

Le due torri hanno la funzione di sorreggere il Plexiglass sull’ultimo piano, su cui verranno applicati vari dispositivi che contribuiscono al funzionamento del Rover. Ce ne saranno due: una per la zona anteriore del Rover e una per la zona posteriore.

CASE BATTERIA

La batteria del Rover sarà posta dentro questo involucro per isolarlo da qualsiasi contatto e stabilizzarlo sul plexiglass.

SCATOLA PER ALIMENTAZIONE

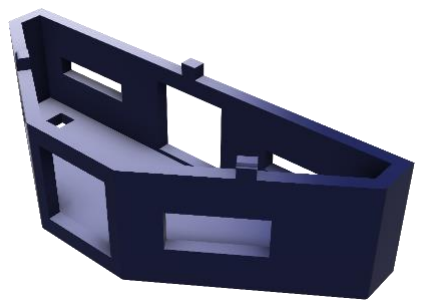
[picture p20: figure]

Posto nella zona anteriore del Rover, questo contenitore avrà dentro di sé il pulsante di alimentazione per la sua accensione.

SUPPORTO SONAR

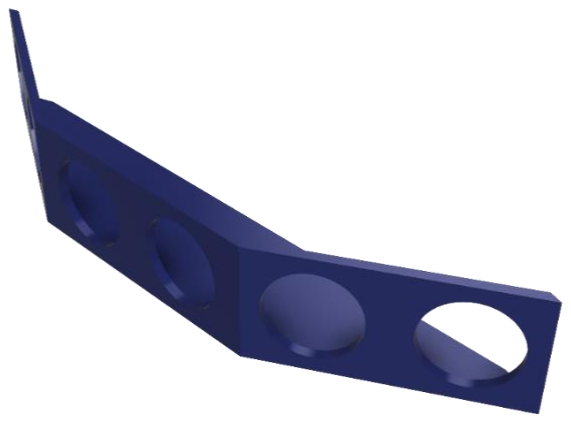
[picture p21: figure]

Nella parte anteriore del Rover si trova il supporto dei sonar. Posta leggermente avanti in modo che il rilevamento ultrasonico sia più preciso.

SUPPORTO PRINCIPALE

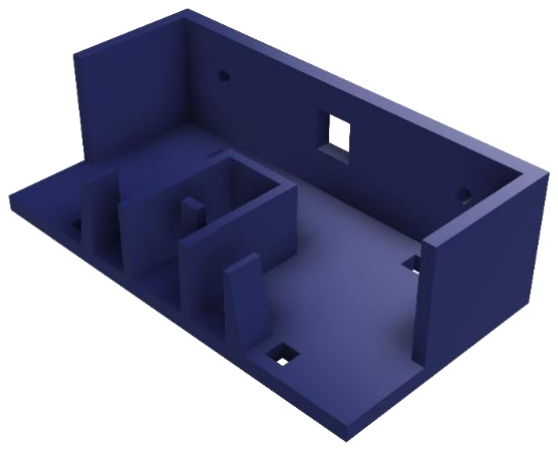
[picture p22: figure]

Nel supporto principale vengono messi i microswitch, il corpo frontale e un modello di applicazione dei baffi affinché possano funzionare in modo ottimale.

# CAPITOLO 2

## CONNESSIONI

In questo capitolo descriveremo le interconnessioni tra i vari componenti.

ARDUINO UNO – SONAR E VOLTMETER

LEFT SONAR

HC-SR04 | Arduino Nano
Echo | 6
Trig | 7
GND | GND
5V | 5V

RIGHT SONAR

HC-SR04 | Arduino Nano
Echo | 4
Trig | 5
GND | GND
5V | 5V

FRONT SONAR

HC-SR04 | Arduino Nano
Echo | 2
Trig | 3
GND | GND
5V | 5V

SCHEMA DI CONNESSIONE

ARDUINO UNO - COMPASS

COMPASS

Il pin di modalità è collegato a GND perché vogliamo utilizzare la modalità di comunicazione seriale. Se vogliamo usare la mossa I2C, lascia semplicemente che questo pin sia scollegato. Il perno di fabbrica viene utilizzato per ripristinare la bussola ai dati di fabbrica.

SCHEMA DI CONNESSIONE:

CMPS11 Pin | Arduino Pin | PMW Pin
GND | GND | No
5V | 5V | No
RX | 6 | Si
TX | 5 | Si
Factory | Non Connesso | No

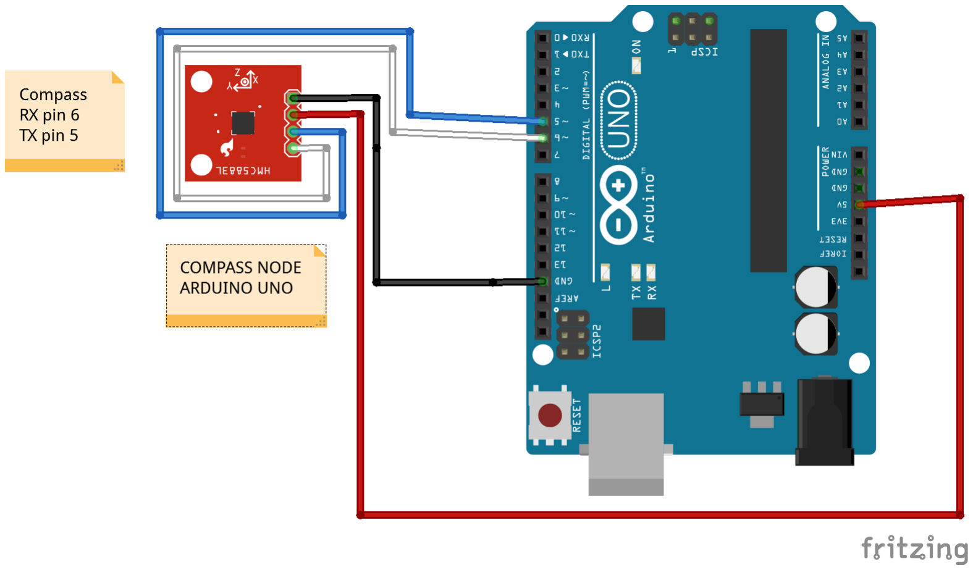
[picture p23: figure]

ARDUINO NANO – MOTOR DRIVER E SWITCH

MOTOR DRIVER SINISTRO

H-L298N | Arduino Pin
GND | Batteria
VCC | Batteria
AIN1 | 2
AIN2 | 4
PWMA | 3

MOTOR DRIVER DESTRO

H-L298N | Arduino Pin
GND | Batteria
VCC | Batteria
BIN1 | 5
BIN2 | 7
PWMB | 6

SWITCH 1

D2F-FL | Arduino Pin | PWM Pin
VCC | 5V | No
No | 8 | Si
Nc | Non Connesso | No

SWITCH 2

D2F-FL | Arduino Pin | PWM Pin
VCC | 5V | No
No | 9 | Si
Nc | Non Connesso | No

SWITCH 3

D2F-FL | Arduino Pin | PWM Pin
VCC | 5V | No
No | 10 | Si
Nc | Non Connesso | No

SCHEMA DI CONNESSIONE:

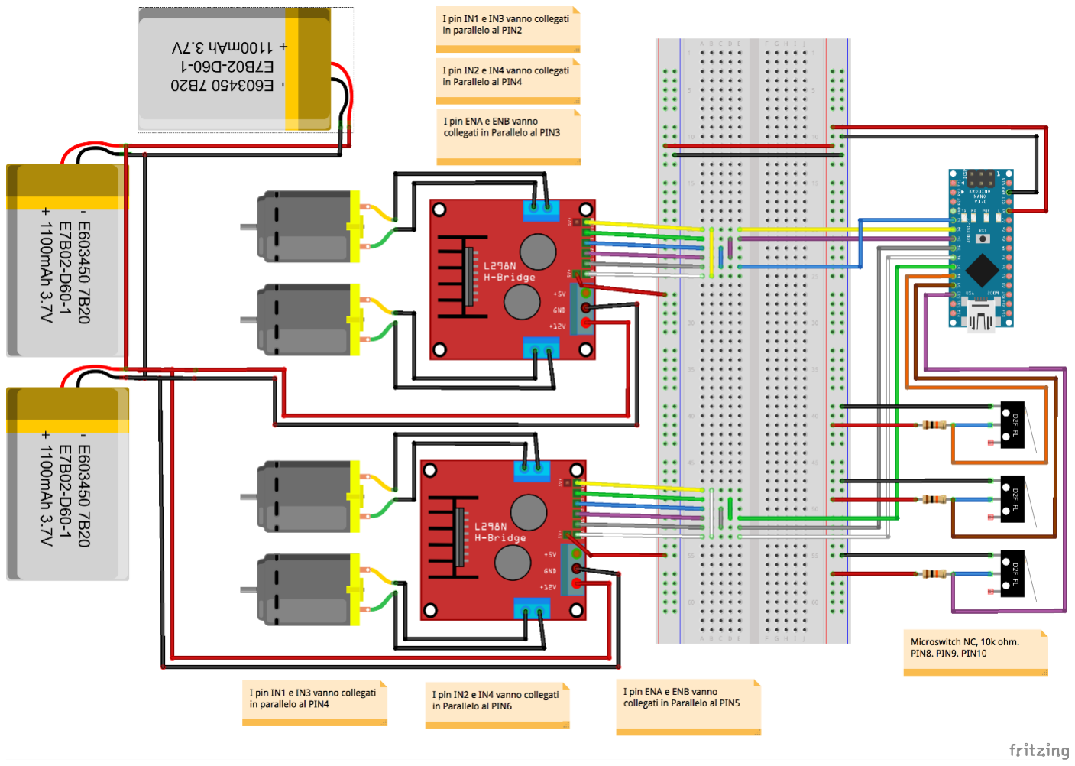
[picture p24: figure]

# CAPITOLO 3

# INTRODUZIONE A ROS

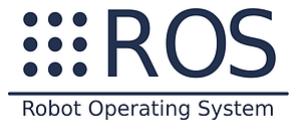
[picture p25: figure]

In questo progetto abbiamo deciso di utilizzare ROS come piattaforma di tutto il sistema.

ROS (Robot Operating System) è un sistema open source. Fornisce i servizi che ci si aspetta da un sistema operativo, tra cui l'astrazione dell'hardware, il controllo dei dispositivi di basso livello, l'implementazione delle funzionalità di uso comune, il passaggio dei messaggi tra i processi e la gestione dei pacchetti. Fornisce inoltre strumenti e librerie per ottenere, creare, scrivere ed eseguire codice su più computer.

Il " | Graph | " runtime di ROS è una rete di processi peer-to-peer (potenzialmente distribuiti su
macchine) che sono accoppiati liberamente usando l'infrastruttura di comunicazione ROS. ROS
implementa diversi stili di comunicazione, tra cui la comunicazione sincrona in stile RPC sui | servizi,
lo streaming asincrono di dati su | argomenti | e la memorizzazione di dati su un | Parameter Server.

ROS non è un framework in real time, sebbene sia possibile integrare ROS con codice in real time.

SISTEMI OPERATIVI SUPPORTATI DA ROS

Attualmente ROS funziona solo su piattaforme basate su Unix. Il software per ROS è principalmente testato su sistemi Ubuntu e Mac OS X, sebbene la comunità ROS abbia contribuito al supporto di Fedora, Gentoo, Arch Linux e altre piattaforme Linux.

Mentre una porta a Microsoft Windows per ROS è possibile, non è stata ancora completamente esplorata.

La versione attuale della distribuzione ROS è Kinetic Kame, installato sul sistema operativo Ubuntu Mate.

ROS LIVELLO FILE SYSTEM

I concetti che Ros ricopre principalmente al livello di filesystem sono le risorse che si incontrano normalmente su disco, come ad esempio:

- Package: i packege sono l'unità principale per l'organizzazione del software in ROS. Un package può contenere processi di runtime ROS (NODI), una libreria dipendente da ROS, set di dati, file di configurazione o qualsiasi altra cosa che sia organizzata in modo utile insieme.
- | Metapackages | : i Metapackage sono package specializzati che servono solo a rappresentare
un gruppo di altri pacchetti correlati. Solitamente i metapackage vengono usati come
supporto di località compatibili con le versioni precedenti per | gli stack
di | rosbuild | convertiti.
- Packages Manifests: Manifests (package.xml) fornisce metadati relativi a un pakage, inclusi nome, versione, descrizione, informazioni sulla licenza, dipendenze e altre meta informazioni come pacchetti esportati. Il manifest del package package.xml è definito
in REP-0127.
- Repository: sono una raccolta di package che condividono un sistema VCS comune. I pacchetti che condividono un VCS condividono la stessa versione e possono essere rilasciati
insieme utilizzando lo strumento di automazione del rilascio di catkin | bloom. Spesso questi
repository si | associano agli stack di | Rosbuild | convertiti. I repository possono contenere
anche un solo pacchetto.
- Tipi di Messaggi (msg): descrizioni dei messaggi, memorizzati in my_package / msg / MyMessageType.msg, definiscono le strutture di dati per i messaggi inviati in ROS.
- Tipi di Servizio (srv): descrizioni del servizio, memorizzate in my_package / srv / MyServiceType.srv, definiscono le strutture dei dati di richiesta e risposta per i servizi in ROS.

ROS COMPUTATION GRAPH LEVEL

Il COMPUTATION GRAPH è la rete peer-to-peer dei processi ROS che stanno elaborando i dati insieme. I concetti di Computation Graph di base di ROS sono NODI, MASTER, PARAMETER SERVER, MESSAGGI, SERVIZI, ARGOMENTI e BORSE, che forniscono tutti i dati al Grafico in diversi modi.

Questi concetti sono implementati nel repository | ros_comm | .
- Nodi: i nodi sono processi che eseguono il calcolo. ROS è progettato per essere modulare su una scala a grana fine; un sistema di controllo robot di solito comprende molti nodi. Ad esempio, un nodo controlla i motori delle ruote, un nodo esegue la localizzazione, un nodo esegue la pianificazione del percorso, un nodo fornisce una vista grafica del sistema e così
via. Un nodo ROS viene scritto con l'uso di una | libreria clientROS, come | roscpp | o | rospy.
- Master: Il master ROS fornisce la registrazione del nome e la ricerca del resto del Graph di calcolo. Senza il Master, i nodi non sarebbero in grado di trovarsi, scambiarsi messaggi o invocare servizi.
- Parameter Server: il Parameter Server consente di memorizzare i dati con la chiave in una posizione centrale. Attualmente fa parte del Master.

- | Messaggi: i nodi comunicano tra loro passando | messaggi. Un messaggio è semplicemente una
struttura dati, comprendente campi tipizzati. Sono supportati i tipi primitivi standard (intero, virgola mobile, booleano, ecc.), Così come le matrici di tipi primitivi. I messaggi possono includere strutture e array arbitrariamente nidificati (molto simili alle strutture C).
- Topic: i messaggi vengono instradati tramite un sistema di trasporto con semantica di pubblicazione / sottoscrizione. Un nodo invia un messaggio PUBBLICANDOLO su un
determinato | topic. Il topic è un | nome | che viene utilizzato per identificare il contenuto del
messaggio. Un nodo interessato a un determinato tipo di dati sarà SOTTOSCRITTO al topic appropriato. Potrebbero esserci più editori e abbonati concorrenti per un singolotopic, e un singolo nodo può pubblicare e / o iscriversi a piùtopic. In generale, gli editori e gli abbonati non sono consapevoli dell'esistenza reciproca. L'idea è di disaccoppiare la produzione di informazioni dal suo consumo. Logicamente, si può pensare ad un argomento come un message bus fortemente tipizzato. Ogni bus ha un nome e chiunque può connettersi al bus per inviare o ricevere messaggi purché siano del tipo giusto.
- Services: Il modello di pubblicazione / sottoscrizione è un paradigma di comunicazione molto flessibile, ma il suo trasporto molti-a-molti, a senso unico, non è appropriato per le interazioni richiesta / risposta, che sono spesso richieste in un sistema distribuito. La
richiesta / risposta viene effettuata tramite i | services | , definiti da una coppia di strutture di
messaggi: uno per la richiesta e uno per la risposta. Un nodo di fornitura offre un servizio
sotto un | nome | e un client utilizza il servizio inviando il messaggio di richiesta e in attesa
della risposta.
- Bags: le bags sono un formato per salvare e riprodurre i dati dei messaggi ROS. I Bags sono un meccanismo importante per la memorizzazione dei dati, come i dati dei sensori.
Il ROS | Master | funge da nameservice nel COMPUTATION GRAPH di ROS. Memorizza gli | topic | e
le informazioni di registrazione dei | servizi | per i | nodi | ROS. I nodi comunicano con il Master per
segnalare le proprie informazioni di registrazione. Poiché questi nodi comunicano con il Master, possono ricevere informazioni su altri nodi registrati e stabilire connessioni appropriate. Il Master effettuerà anche le callback a questi nodi quando queste informazioni di registrazione cambiano, consentendo ai nodi di creare dinamicamente le connessioni man mano che i nuovi nodi vengono eseguiti.

I nodi si connettono direttamente ad altri nodi; il Master fornisce solo informazioni di ricerca, proprio come un server DNS. I nodi che sottoscrivono un argomento richiedono le connessioni dai nodi che pubblicano quell'argomento e stabiliscono tale connessione tramite un protocollo di connessione concordato. Il protocollo più comune utilizzato in un ROS è chiamato TCPROS, che utilizza socket TCP / IP standard.

Funzionamento della comunicazione tra nodi:

Il Nostro Ros Graph è il seguente

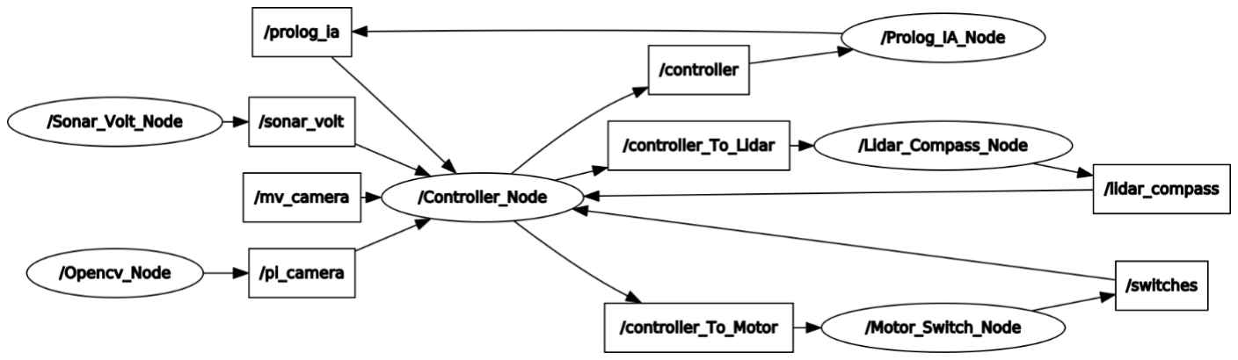
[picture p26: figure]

Il nodo Controller è l’unico a comunciare con tutti gli altri nodi. Ogni nodo (nella figura è un OVALE), per comunicare, pubblica un topic (nella fidura è il RETTANGOLO) al quale si sottoscrive e permette al nodo che riceve il messaggio di leggerlo. Ogni freccetta uscente è un output del messaggio, mentre ogni freccetta entratante è un input di messaggio.

# CODICE

In questo capitolo riporteremo tutti i codici che abbiamo usato, commentati.

### NODI

ARDUINO UNO: COMPASS NODE

1. // libreria ros
2. #include <ros.h>
3. // custom message Compass_Node
4. #include <py_robot/Compass_Node.h>
5. // libreria Servo Motore
6. #include <Servo.h>
7. // libreria seriale di comunicazione con il Compass
8. #include <SoftwareSerial.h>
9.
10. // handle nodon ROS
11. ros::NodeHandle nh;
12.
13. // assegnamento pin Compass
14. #define compassRX 6
15. #define compassTX 5
16.
17. // assegnamento variabili per Compass
18. #define CMPS_GET_ANGLE8 0x12
19. #define CMPS_GET_ANGLE16 0x13
20. #define CMPS_GET_PITCH 0x14
21. #define CMPS_GET_ROLL 0x15
22. #define CMPS_GET_MAG_RAW 0x19
23. #define CMPS_GET_ACCEL_RAW 0x20
24. #define CMPS_GET_GYRO_RAW 0x21

25. #define CMPS_GET_TEMP_RAW 0x22 26.
27. // Servo
28. Servo myservo;
29.
30. // Compass
31. SoftwareSerial cmps11 = SoftwareSerial(compassTX, compassRX); 32.
33. // ROS custom message Compass
34. py_robot::Compass_Node compass_msg;
35.
36. // ROS inizializzazione Pubblisher Compass
37. ros::Publisher pub_compass("compass", &compass_msg); 38.
39. void setup() {
40. // ROS inizializzazione nodo
41. nh.initNode();
42. // ROS creazione Publisher
43. nh.advertise(pub_compass);
44. // inizializzazione seriale per il Compass
45. cmps11.begin(9600);
46. }
47.
48. // funzione lettura Compass
49. // PARAM: CMPS_GET_ANGLE16, CMPS_GET_ANGLE8, CMPS_GET_PITCH, CMPS_GET_ROLL, CMPS_GET _MAG_RAW, CMPS_GET_ACCEL_RAW, CMPS_GET_TEMP_RAW
50. // RETURN
51.
52. void readcompass() {
53. // variabili d'appoggio usate per calcolare gli angolazione a 8 bit e a 16 bit
54. unsigned char high_byte, low_byte, angle8 ;
55. unsigned int angle16;
56.
57. // richiesta e lettura dell'angolo a 16 bit
58. cmps11.write(CMPS_GET_ANGLE16);
59. while (cmps11.available() < 2);
60. high_byte = cmps11.read();
61. low_byte = cmps11.read();
62. // calcolo dell'angolo a 16 bit
63. angle16 = high_byte;
64. angle16 <<= 8;
65. angle16 += low_byte;
66. //assegnamento dell'angolo calcolato nella variabile angle16 del custom message co mpass
67. compass_msg.angle16 = (int)angle16;
68.
69. // richiesta e lettura dell'angolo a 8 bit
70. cmps11.write(CMPS_GET_ANGLE8);
71. while (cmps11.available() < 1);
72. //assegnamento del valore nella variabile angle8 del custom message compass
73. compass_msg.angle8 = (int)cmps11.read();
74.
75. // richiesta e lettura del valore di beccheggio
76. cmps11.write(CMPS_GET_PITCH);
77. while (cmps11.available() < 1);
78. //assegnamento del valore nella variabile pitch del custom message compass
79. compass_msg.pitch = (int)cmps11.read();
80.
81. //richiesta e lettura del valore di rollio
82. cmps11.write(CMPS_GET_ROLL);
83. while (cmps11.available() < 1);
84. //assegnamento del valore nella variabile roll del custom message compass
85. compass_msg.roll = (int)cmps11.read();
86.
87. //richiesta e lettura dei valori del magnetometro
88. cmps11.write(CMPS_GET_MAG_RAW);

89. while (cmps11.available() < 6);
90. //assegnamento dei valori 6 nella variabile array mag del custom message compass
91. compass_msg.mag[0] = (int)cmps11.read();
92. compass_msg.mag[1] = (int)cmps11.read();
93. compass_msg.mag[2] = (int)cmps11.read();
94. compass_msg.mag[3] = (int)cmps11.read();
95. compass_msg.mag[4] = (int)cmps11.read();
96. compass_msg.mag[5] = (int)cmps11.read();
97.
98. //richiesta e lettura dei valori dell'accelerometro
99. cmps11.write(CMPS_GET_ACCEL_RAW);
100. while (cmps11.available() < 6);
101. //assegnamento dei 6 valori nella variabile array acc del custom message co mpass
102. compass_msg.acc[0] = (int)cmps11.read();
103. compass_msg.acc[1] = (int)cmps11.read();
104. compass_msg.acc[2] = (int)cmps11.read();
105. compass_msg.acc[3] = (int)cmps11.read();
106. compass_msg.acc[4] = (int)cmps11.read();
107. compass_msg.acc[5] = (int)cmps11.read(); 108.
109. //richiesta e lettura dei valori del giroscopio
110. cmps11.write(CMPS_GET_GYRO_RAW);
111. while (cmps11.available() < 6)
112. //assegnamento dei 6 valori nella variabile array gyro del custom message compass;
113. compass_msg.gyro[0] = (int)cmps11.read();
114. compass_msg.gyro[1] = (int)cmps11.read();
115. compass_msg.gyro[2] = (int)cmps11.read();
116. compass_msg.gyro[3] = (int)cmps11.read();
117. compass_msg.gyro[4] = (int)cmps11.read();
118. compass_msg.gyro[5] = (int)cmps11.read(); 119.
120. //richiesta e lettura dei valori del termometro
121. cmps11.write(CMPS_GET_TEMP_RAW);
122. while (cmps11.available() < 2);
123. //assegnamento dei 2 valori nella variabile array temp del custom message c ompass;
124. compass_msg.temp = (int)cmps11.read();
125. compass_msg.temp = (int)cmps11.read();
126.
127. delay(100);
128. }
129.
130. void loop() {
131. readcompass();
132. // funzione Publish ROS
133. pub_compass.publish(&compass_msg);
134. // attesa eventi ROS
135. nh.spinOnce();
136. delay(10);
137. }

ARDUINO NANO: MOTOR DRIVER & SWITCH NODE

1. // libreria ros
2. #include <ros.h>
3. // custom message Motor_Switch_Node
4. #include <py_robot/Motor_Switch_Node.h>
5. // custom message Controller_Node

6. #include <py_robot/Controller_To_Motor_Node.h> 7.
8. // handle nodon ROS
9. ros::NodeHandle nh;
10.
11. // assegnamento pin motori 1 e 2
12. #define SXPWM 3
13. #define SXIN1 4
14. #define SXIN2 5
15.
16. // assegnamento pin motori 3 e 4
17. #define DXPWM 6
18. #define DXIN1 7
19. #define DXIN2 8
20.
21.
22. // assegnamento pin switch
23. #define switchFront 11
24. #define switchLeft 10
25. #define switchRight 9
26.
27. // variabili globali
28. String comando;
29. int vel;
30.
31. //funzione callback
32. // PARAM: messaggio ros velo
33.
34. void callback( const py_robot::Controller_To_Motor_Node& velo) {
35. // assegnamento del comando impartito dal Nodo Controller
36. comando = velo.velo;
37.
38. }
39. // funzione sottoscrizione di ros
40. ros::Subscriber<py_robot::Controller_To_Motor_Node> motor_sub("controller_To_Motor", callback);
41.
42. // ros custom message sonar_volt
43. py_robot::Motor_Switch_Node switches;
44.
45. // ros inizializzazione Pubblisher sonar_volt
46. ros::Publisher switch_pub("switches", &switches); 47.
48. // funzione per switch
49. // PARAM: switchpin
50. // RETURN 0 se il lo switch non è attivato, 1 se è attivato 51.
52. void setup() {
53. // inizializzazione nodo
54. nh.initNode();
55. nh.advertise(switch_pub);
56. nh.subscribe(motor_sub); 57.
58. // pin switch
59. pinMode(switchFront, INPUT);
60. pinMode(switchRight, INPUT);
61. pinMode(switchLeft, INPUT);
62. // pin motori 1 e 2 di sinistra
63. pinMode(SXPWM, OUTPUT);
64. pinMode(SXIN1, OUTPUT);
65. pinMode(SXIN2, OUTPUT);
66. analogWrite(SXPWM, 0);
67.
68. // pin motori 3 e 4 di destra
69. pinMode(DXPWM, OUTPUT);
70. pinMode(DXIN1, OUTPUT);

71. pinMode(DXIN2, OUTPUT);
72. analogWrite(DXPWM, 0); 73.
74. delay(1000);
75. }
76.
77. // funzione per switch
78. // PARAM: switchpin
79. // RETURN 0 se il lo switch non è attivato, 1 se è attivato 80.
81. long switchsensor(int switchpin) {
82. // controllo se lo switch è stato premuto
83. if (digitalRead(switchpin) == HIGH) {
84. delay(20);
85. // dopo 20 millisecondi controllo di nuovo se è ancora premuto per evitare error i
86. if (digitalRead(switchpin) == HIGH) {
87. // ritorna 0 se lo switch non è stato attivato
88. return 0;
89. }
90. }
91. // ritorna 1 se lo switch è stato attivato
92. return 1;
93. }
94.
95. // funzioni relative ai comandi da impartire ai motori 96.
97. // funzione Avanti
98. // PARAM: intero vel: parametro velocità
99. // PARAM: intero tempo: parametro tempo di esecuzione
100. void vaiAvanti(int vel, int tempo) {
101. // relativo al motor drive collegato ai motori del lato sinistro
102. digitalWrite(SXIN1, 1);
103. digitalWrite(SXIN2, 0);
104. // velocità lato sinistro
105. analogWrite(SXPWM, vel);
106. // relativo al motor drive collegato ai motori del lato destro
107. digitalWrite(DXIN1, 1);
108. digitalWrite(DXIN2, 0);
109. // velocità lato destro
110. analogWrite(DXPWM, vel); 111.
112. delay(tempo);
113. }
114.
115. // funzione Indietro
116. // PARAM: intero vel: parametro velocità
117. // PARAM: intero tempo: parametro tempo di esecuzione
118. void vaiIndietro(int vel, int tempo) {
119. // relativo al motor drive collegato ai motori del lato sinistro
120. fermo(0);
121. digitalWrite(SXIN1, 0);
122. digitalWrite(SXIN2, 1);
123. // velocità lato sinistro
124. analogWrite(SXPWM, vel);
125. // relativo al motor drive collegato ai motori del lato destro
126. digitalWrite(DXIN1, 0);
127. digitalWrite(DXIN2, 1);
128. // velocità lato destro
129. analogWrite(DXPWM, vel); 130.
131. delay(tempo);
132. fermo(0);
133. }
134.
135. // funzione Sinistra

136. // PARAM: intero vel: parametro velocità
137. // PARAM: intero tempo: parametro tempo di esecuzione
138. void vaiDestra(int vel, int tempo) {
139. // relativo al motor drive collegato ai motori del lato sinistro
140. digitalWrite(SXIN1, 1);
141. digitalWrite(SXIN2, 0);
142. // velocità lato sinistro
143. analogWrite(SXPWM, vel);
144. // relativo al motor drive collegato ai motori del lato destro
145. digitalWrite(DXIN1, 0);
146. digitalWrite(DXIN2, 1);
147. // velocità lato destro
148. analogWrite(DXPWM, vel); 149.
150. delay(tempo);
151. fermo(0);
152. comando = "s";
153. }
154.
155. // funzione Destra
156. // PARAM: intero vel: parametro velocità
157. // PARAM: intero tempo: parametro tempo di esecuzione
158. void vaiSinistra(int vel, int tempo) {
159. // relativo al motor drive collegato ai motori del lato sinistro
160. digitalWrite(SXIN1, 0);
161. digitalWrite(SXIN2, 1);
162. // velocità lato sinistro
163. analogWrite(SXPWM, vel);
164. // relativo al motor drive collegato ai motori del lato destro
165. digitalWrite(DXIN1, 1);
166. digitalWrite(DXIN2, 0);
167. // velocità lato destro
168. analogWrite(DXPWM, vel); 169.
170. delay(tempo);
171. fermo(0);
172. comando = "s";
173. }
174.
175. // funzione Stop
176. // PARAM: intero vel: parametro velocità
177. // PARAM: intero tempo: parametro tempo di esecuzione
178. void fermo(int tempo) {
179. // relativo al motor drive collegato ai motori del lato sinistro
180. digitalWrite(SXIN1, 0);
181. digitalWrite(SXIN2, 0);
182. // velocità lato sinistro
183. analogWrite(SXPWM, 0);
184. // relativo al motor drive collegato ai motori del lato destro
185. digitalWrite(DXIN1, 0);
186. digitalWrite(DXIN2, 0);
187. // velocità lato destro
188. analogWrite(DXPWM, 0); 189.
190. delay(tempo);
191. }
192.
193.
194. void loop() {
195.
196. //switch case con i varin casi possibili dei comandi ricevuti dal Nodo Cont roller
197. switch (comando[0]) {
198.
199. case 'a': vaiAvanti(100, 50);
200. break;

201.
202. case 'b': vaiAvanti(150, 50);
203. break;
204.
205. case 'c': vaiAvanti(200, 50);
206. break;
207.
208. case 'd': vaiAvanti(255, 50);
209. break;
210.
211. case 'e': vaiIndietro(150, 50);
212. break;
213.
214. case 'l': vaiSinistra(255, 200);
215. break;
216.
217. case 'r': vaiDestra(255, 200);
218. break;
219.
220. | case 'f': vaiSinistra(255, 50); | // correzione sinistra
221. break;
222.
223. | case 'g': vaiDestra(255, 50); | // correzione destra
224. break;
225.
226. case 'h': vaiSinistra(255, 2100); // 360 antiorario
227. break;
228.
229. | case 'i': vaiDestra(255, 2100); | //360 orario
230. break;
231.
232. case 'm': vaiSinistra(255, 800); // 90° a sinistra
233. break;
234.
235. | case 'n': vaiDestra(255, 800); | // 90° a destra
236. break;
237.
238. case 'o': vaiSinistra(255, 1200); // 180° a sinistra
239. break;
240.
241. | case 'p': vaiDestra(255, 1200); | // 180° a destra
242. break;
243.
244.
245.
246. case 's': fermo(0);
247. break;
248.
249. }
250.
251. // assegnamento valore, 0 o 1, dello switch centrale nella prima posizione dell'array switches,
252. // prima variabile del custom message Motor_Switch_Node
253. switches.switches[0] = switchsensor(switchFront);
254. // assegnamento valore, 0 o 1, dello switch Sinistra nella seconda posizion e dell'array switches,
255. // prima variabile del custom message Motor_Switch_Node
256. switches.switches[1] = switchsensor(switchLeft);
257. // assegnamento valore, 0 o 1, dello switch Destro nella terza posizione de ll'array switches,
258. // prima variabile del custom message Motor_Switch_Node
259. switches.switches[2] = switchsensor(switchRight);
260. // funzione Publish ROS
261. switch_pub.publish(&switches);
262. // procedura da attuare dopo che uno degli switch viene attivato

263. if (switches.switches[0] == 0 || switches.switches[1] == 0 || switches.swit ches[2] == 0) {
264. // stop
265. fermo(0);
266. // indietro per ___ secondi
267. vaiIndietro(150, 2000);
268. }
269. // attesa eventi ROS
270. nh.spinOnce();
271. delay(10);
272. }

ARDUINO NANO: SONAR & VOLTOMETER NODE

1. // libreria ros
2. #include <ros.h>
3. // custom message Sonar_Volt_Node
4. #include <py_robot/Sonar_Volt_Node.h> 5.
6. // ros
7. ros::NodeHandle nh;
8.
9. // assegnamento dei pin sonar
10. #define echoPinFront 2
11. #define trigPinFront 3
12. #define echoPinRight 4
13. #define trigPinRight 5
14. #define echoPinLeft 6
15. #define trigPinLeft 7
16.
17. // assegnamento pin voltometer
18. #define analogInput 0
19.
20. // variabili voltometer
21. float val;
22. float temp;
23.
24. // ros custom message sonar_volt
25. py_robot::Sonar_Volt_Node sonar_volt_msg;
26.
27. // ros inizializzazione Pubblisher sonar_volt
28. ros::Publisher sonar_volt_pub("sonar_volt", &sonar_volt_msg); 29.
30.
31. void setup() {
32. // inizializzazione nodo
33. nh.initNode();
34. nh.advertise(sonar_volt_pub); 35.
36. // pin sonar
37. pinMode(echoPinFront, INPUT );
38. pinMode(trigPinFront, OUTPUT );
39. pinMode(echoPinRight, INPUT );
40. pinMode(trigPinRight, OUTPUT );
41. pinMode(echoPinLeft, INPUT );
42. pinMode(trigPinLeft, OUTPUT ); 43.
44. // pin voltometer
45. pinMode(analogInput, INPUT);

46.
47. }
48.
49. // funzione per il sonar
50. // PARAM: triggerPin, echoPin
51. // RETURN: distance di tipo long, ritorna la lettura della distanza 52.
53. long sonarsensor(int triggerPin, int echoPin) {
54. long distance = 0;
55. // spengo il trigger
56. digitalWrite(triggerPin, LOW);
57. // accendo il trigger
58. digitalWrite(triggerPin, HIGH);
59. // aspetto 10 millisecondi
60. delayMicroseconds(10);
61. // spengo il trigger
62. digitalWrite(triggerPin, LOW);
63. // tempo ritorno dell'impulso
64. long times = pulseIn(echoPin, HIGH);
65. // se il tempo non supera 38000 abbiamo perso l'impulso e ritornerà 0
66. if (times < 38000) {
67. // calcolo della distanza
68. distance = 0.034 * times / 2;
69. // ritorno la distanza
70. return distance;
71. }
72. // ritorno la distanza = 0
73. return distance;
74. }
75.
76. // funzione voltometer
77. // RETURN: val di tipo float, ritorna voltaggio in imput dalla batteria 78.
79. float voltometer() {
80. // lettura segnale
81. val=analogRead(0);
82. // operazione di conversione segnale imput in volt
83. temp=val/40.92;
84. // sottraggo margine di errore
85. val=temp - 0.7;
86. // ritorno valore volt
87. return val;
88. }
89.
90. void loop() {
91. // assegnamento valore del sonar centrale nella prima posizione dell'array sonar,
92. // prima variabile del custom message Sonar_Volt
93. sonar_volt_msg.sonar[0] = sonarsensor(trigPinFront, echoPinFront);
94. // assegnamento valore del sonar destro nella seconda posizione dell'array sonar,
95. // prima variabile del custom message Sonar_Volt
96. sonar_volt_msg.sonar[1] = sonarsensor(trigPinRight, echoPinRight);
97. // assegnamento valore del sonar sinistro nella terza posizione dell'array sonar,
98. // prima variabile del custom message Sonar_Volt
99. sonar_volt_msg.sonar[2] = sonarsensor(trigPinLeft, echoPinLeft);
100. // funzione del voltometro e assegnamento nella seconda variabile del custo m message
101. sonar_volt_msg.volt = voltometer();
102. // funzione Publish ros
103. sonar_volt_pub.publish(&sonar_volt_msg);
104. // attesa eventi ROS
105. nh.spinOnce();
106. delay(10);
107. }

CONTROLLER NODE

1. #! /usr/bin/python
2. import rospy
3. import roslaunch.rlutil
4. import roslaunch.parent
5. import roslaunch
6. import py_robot.msg as PyRobot
7. import time
8.
9. controller_msg = PyRobot.Controller_Node()
10. controller_to_motor_msg = PyRobot.Controller_To_Motor_Node() 11.
12. angle16 = None
13. angle8 = None
14. pitch = None
15. roll = None
16. mag = [None for x in range(0, 6)]
17. acc = [None for x in range(0, 6)]
18. gyro = [None for x in range(0, 6)]
19. temp = None
20. comando = None
21. switch = [None for x in range(0, 3)]
22. sonar = [None for x in range(0, 3)]
23. volt = None
24. eureca = None
25. visione = None
26. launch = None
27. risposta_prolog = None 28.
29.
30. def resetvar():
31. """
32. Funzione che setta le variabili a nullo per evitare l'invio di messaggi non comp leti.
33. Lavora sulle variabili globali angle16, angle8, pitch, roll, mag, acc, gyro,
34. temp, comando, switch, sonar, volt, eureca e visione
35. :return: nulla
36. """
37. global angle16, angle8, pitch, roll, mag, acc, gyro, temp, switch, sonar, volt, eureca, visione, \
38. comando, risposta_prolog
39.
40. angle16 = None
41. angle8 = None
42. pitch = None
43. roll = None
44. mag = [None for x in range(0, 6)]
45. acc = [None for x in range(0, 6)]
46. gyro = [None for x in range(0, 6)]
47. temp = None
48. comando = None
49. switch = [None for x in range(0, 3)]
50. sonar = [None for x in range(0, 3)]
51. volt = None
52. eureca = None
53. visione = None
54. risposta_prolog = None 55.
56.
57. def callback_prolog(msg):

58. """
59. funzione di callback per i messaggi provenienti dal nodo Prolog_IA,
60. modifica la variabile globale comando
61. :param msg: messagio ricevuto
62. :return: nulla
63. """
64. global comando, risposta_prolog 65.
66. risposta_prolog = msg.risposta 67.
68. comando = ''
69. risposta_prolog = msg.risposta
70. if risposta_prolog == "dritto":
71. comando = "e"
72. elif risposta_prolog == "destra":
73. comando = "r"
74. elif risposta_prolog == "sinistra":
75. comando = "q"
76. elif risposta_prolog == "indietro":
77. comando = "i"
78. elif risposta_prolog == "stop":
79. comando = "s"
80. elif risposta_prolog == "correggi_a_destra":
81. comando = "t"
82. elif risposta_prolog == "correggi_a_sinistra":
83. comando = "u"
84. elif risposta_prolog == "fine":
85. endfunction()
86. else:
87. comando = 's'
88.
89.
90. def startfunction():
91. """
92. Funzione di inizio programma. Si occupa di far partire i nodi
93. :return: nulla
94. """
95. uuid = roslaunch.rlutil.get_or_generate_uuid(None, False)
96. roslaunch.configure_logging(uuid)
97. launch = roslaunch.parent.ROSLaunchParent(uuid, [
98. "../launch/node_launcher.launch"]) # qui da aggiornare con il path del file launch
99. launch.start()
100. rospy.loginfo("started")
101.
102.
103. def endfunction():
104. """
105. Funzione di fine programma. Si occupa di far terminare il Nodo Controller
106. :return: nulla
107. """
108. global comando
109. launch.shutdown()
110. time.sleep(1)
111. rospy.signal_shutdown('Mission Complete') 112.
113.
114. def callback_switch(msg):
115. """
116. Funzione Callback che processa i dati inviati dai Nodo Motor_Switch
117. :param msg: messaggio ROS dal Nodo Motor_Switch
118. :return: nulla
119. """
120. global switch
121. switch = msg.switches

122. rospy.loginfo(switch) 123.
124.
125. def callback_sonar_volt(msg):
126. """
127. Funzione Callback che processa i dati inviati dai Nodo Sonar_Volt
128. :param msg: messaggio ROS dal Nodo Sonar_Volt
129. :return: nulla
130. """
131. global sonar, volt
132. sonar = msg.sonar
133. volt = msg.volt
134.
135.
136. def callback_compass(msg):
137. """
138. Funzione Callback che processa i dati inviati dai Nodo Compass
139. :param msg: messaggio ROS dal Nodo Compass
140. """
141. global angle16, angle8, pitch, roll, mag, acc, gyro, temp
142. angle16 = msg.angle16
143. angle8 = msg.angle8
144. pitch = msg.pitch
145. roll = msg.roll
146. mag = msg.mag
147. acc = msg.acc
148. gyro = msg.gyro
149. temp = msg.temp
150.
151.
152. def callback_mvcamera(msg):
153. """
154. Funzione Callback che processa i dati inviati dai Nodo MV_Camera
155. :param msg: messaggio ROS dal Nodo MV_Camera
156. :return: nulla
157. """
158. global eureca
159. eureca = msg.eureca
160.
161.
162. def callback_pi_camera(msg):
163. """
164. Funzione Callback che processa i dati inviati dai Nodo PI_Camera
165. :param msg: messaggio ROS dal Nodo PI_Camera
166. :return: nulla
167. """
168. global visione
169. visione = msg.visione
170.
171.
172. def ifNotNone(angle16, angle8, pitch, roll, mag, acc, gyro, temp, volt, sonar , visione, risposta_prolog, switch):
173. """
174. funzione di controlo delle variabili globali,
175. controlla se sono state modificate tutte
176. :param risposta_prolog:
177. :param visione:
178. :param angle16: misura del angolo a 16
179. :param angle8: misura del angolo a 8
180. :param pitch: misura del pitch
181. :param roll: misura del roll
182. :param mag: misura del mag
183. :param acc: misura del acc
184. :param gyro: misura del gyro
185. :param temp: misura della temperatura
186. :param comando: variabile del comando da inviare

187. :param volt: misura della batteria
188. :param sonar: misura dei sonar
189. :return: True se sono modificate, False se sono ancora None
190. """
191.
192. return angle16 is not None and angle8 is not None and pitch is not None a nd roll is not None \
193. and mag is not None and acc is not None and gyro is not None and t emp is not None \
194. and volt is not None and sonar is not None and visione is not None \
195. and risposta_prolog is not None and not switch == [None, None, Non e]
196.
197.
198. def main():
199. """
200. Funzione principale che si occupa di inizializzare il Nodo, i Pubblisher e i Subscriber. Si occupa anche di salvare
201. i valori ricevuti dai vari Nodi nei mesaggi Controller_Node.msg
202. :return: nulla
203. """
204. global angle16, angle8, pitch, roll, mag, acc, gyro, temp, switch, sonar, volt, eureca, visione, \
205. comando, risposta_prolog
206. # inizializzazione nodo Controller
207. rospy.init_node("Controller_Node", disable_signals=True)
208. startfunction()
209. # inizializzazioni Publisher e Subsciber
210. controller_pub = rospy.Publisher("controller", PyRobot.Controller_Node, q ueue_size=1)
211. controller_to_motor_pub = rospy.Publisher("controller_To_Motor", PyRobot. Controller_To_Motor_Node, queue_size=1)
212. rospy.Subscriber("prolog", PyRobot.Prolog_IA_Node, callback_prolog)
213. rospy.Subscriber("switches", PyRobot.Motor_Switch_Node, callback_switch)
214. rospy.Subscriber("sonar_volt", PyRobot.Sonar_Volt_Node, callback_sonar_vo lt)
215. rospy.Subscriber("mv_camera", PyRobot.MV_Camera_Node, callback_mvcamera)
216. rospy.Subscriber("compass", PyRobot.Compass_Node, callback_compass)
217. rospy.Subscriber("pi_camera", PyRobot.Pi_Camera_Node, callback_pi_camera)
218. r = rospy.Rate(1)
219. while not rospy.is_shutdown():
220. if ifNotNone(angle16, angle8, pitch, roll, mag, acc, gyro, temp, volt , sonar, visione, risposta_prolog, switch):
221. controller_msg.angle16 = angle16 # messaggio per il nodo Prolog per angle16
222. controller_msg.angle8 = angle8 # messaggio per il nodo Prolog pe r angle8
223. controller_msg.pitch = pitch # messaggio per il nodo Prolog per pitch
224. controller_msg.roll = roll # messaggio per il nodo Prolog per ro ll
225. controller_msg.mag = mag # messaggio per il nodo Prolog per mag
226. controller_msg.acc = acc # messaggio per il nodo Prolog per acc
227. controller_msg.gyro = gyro # messaggio per il nodo Prolog per gy ro
228. controller_msg.temp = temp # messaggio per il nodo Prolog per te mp
229. controller_msg.switches = switch # messaggio per il nodo Prolog per switch

230. controller_msg.volt = volt # messaggio per il nodo Prolog per vo lt
231. controller_msg.sonar = sonar # messaggio per il nodo Prolog per sonar
232. controller_msg.visione = visione # messaggio per il nodo Prolog per Py Camera
233.
234. if eureca == 'trovato':
235. controller_msg.qrcode = 1 # messaggio per il nodo Prolog per qrcode
236.
237. if comando is not None:
238. controller_to_motor_msg.velo = comando # messaggio per il no do Motor_Switch per Motor
239.
240. # funzioni Publish ROS
241. controller_pub.publish(controller_msg)
242. controller_to_motor_pub.publish(controller_to_motor_msg) 243.
244. resetvar()
245. r.sleep()
246.
247.
248. if __name__ == '__main__':
249. try:
250. main()
251. except rospy.ROSInterruptException:
252. pass

OPEN_MV NODE

1. global sonar, volt
2. sonar = msg.sonar
3. volt = msg.volt
4.
5.
6. def callback_compass(msg):
7. """
8. Funzione Callback che processa i dati inviati dai Nodo Compass
9. :param msg: messaggio ROS dal Nodo Compass
10. """
11. global angle16, angle8, pitch, roll, mag, acc, gyro, temp
12. angle16 = msg.angle16
13. angle8 = msg.angle8
14. pitch = msg.pitch
15. roll = msg.roll
16. mag = msg.mag
17. acc = msg.acc
18. gyro = msg.gyro
19. temp = msg.temp
20.
21.
22. def callback_mvcamera(msg):
23. """
24. Funzione Callback che processa i dati inviati dai Nodo MV_Camera
25. :param msg: messaggio ROS dal Nodo MV_Camera
26. :return: nulla
27. """
28. global eureca
29. eureca = msg.eureca
30.
31.

32. def callback_pi_camera(msg):
33. """
34. Funzione Callback che processa i dati inviati dai Nodo PI_Camera
35. :param msg: messaggio ROS dal Nodo PI_Camera
36. :return: nulla
37. """
38. global visione
39. visione = msg.visione
40.
41.
42. def ifNotNone(angle16, angle8, pitch, roll, mag, acc, gyro, temp, volt, sonar, visio ne, risposta_prolog, switch):
43. """
44. funzione di controlo delle variabili globali,
45. controlla se sono state modificate tutte
46. :param risposta_prolog:
47. :param visione:
48. :param angle16: misura del angolo a 16
49. :param angle8: misura del angolo a 8
50. :param pitch: misura del pitch
51. :param roll: misura del roll
52. :param mag: misura del mag
53. :param acc: misura del acc
54. :param gyro: misura del gyro
55. :param temp: misura della temperatura
56. :param comando: variabile del comando da inviare
57. :param volt: misura della batteria
58. :param sonar: misura dei sonar
59. :return: True se sono modificate, False se sono ancora None
60. """
61.
62. return angle16 is not None and angle8 is not None and pitch is not None and roll is not None \
63. and mag is not None and acc is not None and gyro is not None and temp is not None \
64. and volt is not None and sonar is not None and visione is not None \
65. and risposta_prolog is not None and not switch == [None, None, None] 66.
67.
68. def main():
69. """
70. Funzione principale che si occupa di inizializzare il Nodo, i Pubblisher e i Sub scriber. Si occupa anche di salvare
71. i valori ricevuti dai vari Nodi nei mesaggi Controller_Node.msg
72. :return: nulla
73. """
74. global angle16, angle8, pitch, roll, mag, acc, gyro, temp, switch, sonar, volt, eureca, visione, \
75. comando, risposta_prolog
76. # inizializzazione nodo Controller
77. rospy.init_node("Controller_Node", disable_signals=True)
78. startfunction()
79. # inizializzazioni Publisher e Subsciber
80. controller_pub = rospy.Publisher("controller", PyRobot.Controller_Node, queue_si ze=1)
81. controller_to_motor_pub = rospy.Publisher("controller_To_Motor", PyRobot.Control ler_To_Motor_Node, queue_size=1)
82. rospy.Subscriber("prolog", PyRobot.Prolog_IA_Node, callback_prolog)
83. rospy.Subscriber("switches", PyRobot.Motor_Switch_Node, callback_switch)
84. rospy.Subscriber("sonar_volt", PyRobot.Sonar_Volt_Node, callback_sonar_volt)
85. rospy.Subscriber("mv_camera", PyRobot.MV_Camera_Node, callback_mvcamera)
86. rospy.Subscriber("compass", PyRobot.Compass_Node, callback_compass)
87. rospy.Subscriber("pi_camera", PyRobot.Pi_Camera_Node, callback_pi_camera)
88. r = rospy.Rate(1)
89. while not rospy.is_shutdown():

90. if ifNotNone(angle16, angle8, pitch, roll, mag, acc, gyro, temp, volt, sonar , visione, risposta_prolog, switch):
91. controller_msg.angle16 = angle16 # messaggio per il nodo Prolog per ang le16
92. controller_msg.angle8 = angle8 # messaggio per il nodo Prolog per angle 8
93. controller_msg.pitch = pitch # messaggio per il nodo Prolog per pitch
94. controller_msg.roll = roll # messaggio per il nodo Prolog per roll
95. controller_msg.mag = mag # messaggio per il nodo Prolog per mag
96. controller_msg.acc = acc # messaggio per il nodo Prolog per acc
97. controller_msg.gyro = gyro # messaggio per il nodo Prolog per gyro
98. controller_msg.temp = temp # messaggio per il nodo Prolog per temp
99. controller_msg.switches = switch # messaggio per il nodo Prolog per swi tch
100. controller_msg.volt = volt # messaggio per il nodo Prolog per vo lt
101. controller_msg.sonar = sonar # messaggio per il nodo Prolog per sonar
102. controller_msg.visione = visione # messaggio per il nodo Prolog per Py Camera
103.
104. if eureca == 'trovato':
105. controller_msg.qrcode = 1 # messaggio per il nodo Prolog per qrcode
106.
107. if comando is not None:
108. controller_to_motor_msg.velo = comando # messaggio per il no do Motor_Switch per Motor
109.
110. # funzioni Publish ROS
111. controller_pub.publish(controller_msg)
112. controller_to_motor_pub.publish(controller_to_motor_msg) 113.
114. resetvar()
115. r.sleep()
116.
117.
118. if __name__ == '__main__':
119. try:
120. main()
121. except rospy.ROSInterruptException:
122. pass

OPEN_CV NODE

1. #! /usr/bin/python
2.
3. from picamera.array import PiRGBArray
4. from picamera import PiCamera
5. import cv2
6. import numpy as np
7. import time
8. import py_robot.msg as PyRobot
9. import rospy
10.
11. pi_camera_msg = PyRobot.Pi_Camera_Node() 12.
13. camera = PiCamera()
14. camera.resolution = (640, 480)
15. rawCapture = PiRGBArray(camera)

16. time.sleep(0.1)
17.
18.
19. def imgs():
20. global camera, rawCapture
21. camera.capture(rawCapture, format="bgr")
22. image = rawCapture.array
23. ris = cv2.Canny(image, 100, 200)
24. misura = np.array([])
25. height, width = ris.shape
26. ris1 = ris.copy()
27. for x in range(width - 1):
28. for h in range(height - 1):
29. hei = height - h - 1
30. if ris1[hei, x] == 255:
31. misura = np.append(misura, int(hei))
32. break
33. else:
34. ris1.itemset((hei, x), 50)
35. misura = np.split(misura, [90, 220])
36. media_sinistra = np.median(misura[0])
37. media_centrale = np.median(misura[1])
38. media_destra = np.median(misura[2])
39. print(media_sinistra, media_centrale, media_destra)
40. rawCapture.truncate(0)
41. if media_sinistra < media_centrale:
42. if (media_sinistra < media_destra):
43. print("vai a sinistra: ", media_sinistra)
44. return "sinistra"
45. else:
46. print("vai a destra: ", media_destra)
47. return "destra"
48. elif media_centrale < media_destra:
49. print("continua dritto: ", media_centrale)
50. return "centro"
51. else:
52. print("vai a destra: ", media_destra)
53. return "destra"
54.
55.
56. def main():
57. rospy.init_node("Pi_Camera_Node", disable_signals=True)
58. pi_camera_pub = rospy.Publisher("pi_camera_pub", PyRobot.Pi_Camera_Node, queue_s ize=1)
59. r = rospy.Rate(1)
60. while not rospy.is_shutdown():
61. pi_camera_msg.visione = imgs()
62. pi_camera_pub.publish(pi_camera_msg)
63. r.sleep()
64.
65.
66. if __name__ == '__main__':
67. try:
68. main()
69. except rospy.ROSInterruptException:
70. pass

PROLOG_IA_NODE

1. #! /usr/bin/python

2.
3. import pyswip.prolog
4. import py_robot.msg as PyRobot
5. import rospy
6. import time
7. import numpy as np
8.
9. prolog_msg = PyRobot.Prolog_IA_Node() 10.
11. prolog = None
12. commandolder = "avanti"
13. oldangle = None
14.
15.
16. # var global
17. qrcode = None
18. fotocamera = None
19. switch = None
20. sonar = None
21. volt = None
22. lidar = None
23. angle16 = None
24. angle8 = None
25. pitch = None
26. roll = None
27. mag = None
28. acc = None
29. gyro = None
30. temp = None
31. lidarm = None
32.
33.
34. def resetNone():
35. """
36. Funzione per il reset delle variabili ambientali
37. :return:
38. """
39. global qrcode, fotocamera, switch, sonar, volt, lidar, angle16, angle8, pitch, r oll, mag, acc, gyro, temp
40. qrcode = None
41. fotocamera = None
42. switch = None
43. sonar = None
44. volt = None
45. lidar = None
46. angle16 = None
47. angle8 = None
48. pitch = None
49. roll = None
50. mag = None
51. acc = None
52. gyro = None
53. temp = None
54.
55.
56. def prologinit_and_rules():
57. """
58. Funzione per l'inizializzazione di prolog e la creazione delle regole
59. :return: nulla
60. """
61. global prolog
62.
63. ###########################
64. # INIZIALIZZAZIONE PROLOG #
65. ########################### 66.

67. prolog = pyswip.Prolog() 68.
69. ###########################
70. # CREAZIONE COMANDI ROVER #
71. ###########################
72.
73. # comandi disponibili
74. prolog.assertz("command(avanti, 1)")
75. prolog.assertz("command(sinistra, 2)")
76. prolog.assertz("command(destra, 3)")
77. prolog.assertz("command(indietro,4)")
78. prolog.assertz("command(stop, 5)")
79. prolog.assertz("command(fine, 6)")
80. prolog.assertz("command(batteria, 7)")
81. prolog.assertz("command(correggi_a_destra, 8)")
82. prolog.assertz("command( correggi_a_sinistra, 9)") 83.
84. #############################
85. # CREAZIONE REGOLE GENERALI #
86. #############################
87.
88. # regola per gli switch false se sbatte true se non sbatte
89. prolog.assertz("switch(_):- switch(sinistra,X), switch(centro,Y), switch(destra, Z), X == 0, Y == 0, Z == 0, !")
90.
91. # regola per il cambio direzione
92. prolog.assertz("distancetrue(_):- sonar(destra, A), sonar(centro, B), sonar(sini stra, C), A > 50, B > 50, C > 50, !")
93.
94. # regola per il cambio direzione (indietro) a una certa distanza da un possibile ostacolo troppo vicino
95. prolog.assertz("sonartrue(_):- sonar(destra, A), sonar(centro, B), sonar(sinistr a, C), A > 30, B > 30, C > 30, !")
96.
97. # regola per capire quale e' il sonar con la distanza maggiore
98. prolog.assertz("sonar(Y) :- sonar(centro, A), sonar(destra, B), sonar(sinistra, C), D is max(A, B),"
99. " X is max(D, C), sonar(Y, X),!")
100.
101. # regola per capire quale e' il sonar tra destra e sinistra maggiore
102. prolog.assertz("sonardxsx(Y):- sonar(destra, A), sonar(sinistra, B), X is max(A, B), sonar(Y, X), Y \== centro, !")
103.
104. # regola per le condizioni necessarie per il cambio di qualasiasi direzio ne
105. prolog.assertz("condictrue(_):- switch(_), volt(Y), Y>11, qrcode(Q), Q == 0, !")
106.
107. # commando batteria
108. prolog.assertz("command(X):- volt(Y), Y < 11, C is 7, command(X, C),!") 109.
110. # comando fine
111. prolog.assertz("command(X):- qrcode(1), C is 6, command(X,C),!")
112.
113. # comando correggi a destra
114. prolog.assertz("command(X):-
commandolder(O), O == avanti, condictrue(_), distancetrue(_), angle8(A), oldangle8(B ),"
115. " S is A-B, S > 10, command(X, 8),!")
116.
117. # comando correggi a sinistra
118. prolog.assertz("command(X):-
commandolder(O), O == avanti, condictrue(_), distancetrue(_), angle8(A), oldangle8(B ),"
119. " S is B-A, S > 10, command(X, 9),!")
120.

121. # comando indietro
122. prolog.assertz("command(X):- commandolder(O), O \== indietro, \+ sonartru e(_), volt(Y), Y > 11,"
123. " qrcode(Q), Q == 0, command(X,4),!")
124. prolog.assertz("command(X):- commandolder(O), O \== indietro, switch(_,1) , volt(Y), Y > 11,"
125. " qrcode(Q), Q == 0, command(X,4),!")
126.
127. # comando avanti
128. prolog.assertz("command(X):- commandolder(O), O == avanti, condictrue(_), distancetrue(_), command(X,1), !")
129. prolog.assertz("command(X):- commandolder(O), O \== indietro, condictrue( _), distancetrue(_), sonar(U), "
130. "U == centro, fotocamera(F), F == centro, command(X,1), !" )
131. prolog.assertz("command(X):- commandolder(O), O \== indietro, condictrue( _), distancetrue(_),"
132. " sonar(U), U == centro, command(X,1), !")
133. prolog.assertz("command(X):- commandolder(O), O \== indietro, condictrue( _), distancetrue(_), command(X,1), !")
134.
135. # comando sinistra
136. prolog.assertz("command(X):- condictrue(_), sonartrue(_), sonardxsx(U), U == sinistra, fotocamera(F),"
137. " F == sinistra, command(X,2),!")
138. prolog.assertz("command(X):- condictrue(_), sonartrue(_), sonardxsx(U), U == sinistra, command(X,2),!")
139.
140. # comando destra
141. prolog.assertz("command(X):- condictrue(_), sonartrue(_), sonardxsx(U), U == destra, fotocamera(F),"
142. " F == destra, command(X,3), !")
143. prolog.assertz("command(X):- condictrue(_), sonartrue(_), sonardxsx(U), U == destra, command(X,3) ,!")
144.
145. # comando indietro che viene eseguito quando non c'e' spazio per girare a destra o a sinista
146. prolog.assertz("command(X):- \+ sonartrue(_), volt(Y), Y > 11, qrcode(Q), Q == 0, command(X,4),!")
147.
148. # comando stop (errore)
149. prolog.assertz("command(X):- command(X,5),!")
150.
151.
152. def prologIA(commandolder, qrcode, fotocamera, switch, sonar, volt, lidar,
153. angle16, angle8, pitch, roll, mag, acc, gyro, temp, oldangle, li darm):
154. """
155. Funzione per il caricamento dei fatti, per esecuzione delle query e della demolizione dei fatti caricati
156. :param commandolder: vecchio comando di default e' avanti
157. :param qrcode: 0 per non trovato 1 per trovato
158. :param fotocamera: vale sinistra o destra o centro e identifica lo spazio libero
159. :param switch: 0 se non attivo 1 per attivo e' un arry di 3 elementi
160. :param sonar: vale la misurazione effettuata e' un array di 3 elementi
161. :param volt: vale la misurazione effettuata
162. :param lidar: vale le misurazioni effettuate e' un array di 19 elementi
163. :param angle16: vale la misurazione effettuata
164. :param angle8: vale la misurazione effettuata
165. :param pitch: vale la misurazione effettuata
166. :param roll: vale la misurazione effettuata
167. :param mag: vale le misurazioni effettuate e' un array di 6 elementi
168. :param acc: vale le misurazioni effettuate e' un array di 6 elementi
169. :param gyro: vale le misurazioni effettuate e' un array di 6 elementi
170. :param temp: vale la misurazione effettuata

171. :param oldangle: vale un angolo iniziale
172. :return: resultato della query
173. """
174. global prolog
175.
176. ###################
177. # CREAZIONE FATTI #
178. ###################
179.
180. # comando vecchio
181. prolog.assertz("commandolder(" + str(commandolder) + ")") 182.
183. # qrcode: 0 per false 1 per true
184. prolog.assertz("qrcode(" + str(qrcode) + ")")
185.
186. # fotocomera
187. prolog.assertz("fotocamera(" + str(fotocamera) + ")") 188.
189. # switch
190. prolog.assertz("switch(centro, " + str(switch[1]) + ")")
191. prolog.assertz("switch(sinistra, " + str(switch[0]) + ")")
192. prolog.assertz("switch(destra, " + str(switch[2]) + ")")
193.
194. # sonar: mettere prima il centro cosi se sono 3 sonar uguali il sistema p rendera il primo e quindi va avanti
195. prolog.assertz("sonar(centro, " + str(sonar[1]) + ")")
196. prolog.assertz("sonar(sinistra, " + str(sonar[0]) + ")")
197. prolog.assertz("sonar(destra, " + str(sonar[2]) + ")") 198.
199. # volt
200. prolog.assertz("volt(" + str(volt) + ")")
201.
202. # compass
203. prolog.assertz("angle16(" + str(angle16) + ")")
204. prolog.assertz("angle8(" + str(angle8) + ")")
205. prolog.assertz("pitch(" + str(pitch) + ")")
206. prolog.assertz("roll(" + str(roll) + ")")
207. prolog.assertz("mag(xhigh, " + str(mag[0]) + ")")
208. prolog.assertz("mag(xlow, " + str(mag[1]) + ")")
209. prolog.assertz("mag(yhigh, " + str(mag[2]) + ")")
210. prolog.assertz("mag(ylow, " + str(mag[3]) + ")")
211. prolog.assertz("mag(zhigh, " + str(mag[4]) + ")")
212. prolog.assertz("mag(zlow, " + str(mag[5]) + ")")
213. prolog.assertz("acc(xhigh, " + str(acc[0]) + ")")
214. prolog.assertz("acc(xlow, " + str(acc[1]) + ")")
215. prolog.assertz("acc(yhigh, " + str(acc[2]) + ")")
216. prolog.assertz("acc(ylow, " + str(acc[3]) + ")")
217. prolog.assertz("acc(zhigh, " + str(acc[4]) + ")")
218. prolog.assertz("acc(zlow, " + str(acc[5]) + ")")
219. prolog.assertz("gyro(xhigh, " + str(gyro[0]) + ")")
220. prolog.assertz("gyro(xlow, " + str(gyro[1]) + ")")
221. prolog.assertz("gyro(yhigh, " + str(gyro[2]) + ")")
222. prolog.assertz("gyro(ylow, " + str(gyro[3]) + ")")
223. prolog.assertz("gyro(zhigh, " + str(gyro[4]) + ")")
224. prolog.assertz("gyro(zlow, " + str(gyro[5]) + ")")
225. prolog.assertz("temp(" + str(temp) + ")")
226.
227. # angolo vecchio
228. prolog.assertz("oldangle8(" + str(oldangle) + ")")
229.
230. ######################################################################### ##########################################
231.
232. ##########################
233. # ESEQUZIONE DELLA QUERY #
234. ##########################

235.
236. result = list(prolog.query("command(Result)"))
237.
238. ######################################################################### ##########################################
239.
240. #################################
241. # DEMOLIZIONE DEI FATTI CARICATI#
242. #################################
243.
244. # comando vecchio
245. prolog.retract("commandolder(" + str(commandolder) + ")") 246.
247. # qrcode: 0 per false 1 per true
248. prolog.retract("qrcode(" + str(qrcode) + ")")
249.
250. # fotocomera
251. prolog.retract("fotocamera(" + str(fotocamera) + ")") 252.
253. # switch
254. prolog.retract("switch(centro, " + str(switch[1]) + ")")
255. prolog.retract("switch(sinistra, " + str(switch[0]) + ")")
256. prolog.retract("switch(destra, " + str(switch[2]) + ")")
257.
258. # sonar: mettere prima il centro cosi se sono 3 sonar uguali il sistema p rendera il primo e quindi va avanti
259. prolog.retract("sonar(centro, " + str(sonar[1]) + ")")
260. prolog.retract("sonar(sinistra, " + str(sonar[0]) + ")")
261. prolog.retract("sonar(destra, " + str(sonar[2]) + ")") 262.
263. # volt
264. prolog.retract("volt(" + str(volt) + ")")
265.
266. # compass
267. prolog.retract("angle16(" + str(angle16) + ")")
268. prolog.retract("angle8(" + str(angle8) + ")")
269. prolog.retract("pitch(" + str(pitch) + ")")
270. prolog.retract("roll(" + str(roll) + ")")
271. prolog.retract("mag(xhigh, " + str(mag[0]) + ")")
272. prolog.retract("mag(xlow, " + str(mag[1]) + ")")
273. prolog.retract("mag(yhigh, " + str(mag[2]) + ")")
274. prolog.retract("mag(ylow, " + str(mag[3]) + ")")
275. prolog.retract("mag(zhigh, " + str(mag[4]) + ")")
276. prolog.retract("mag(zlow, " + str(mag[5]) + ")")
277. prolog.retract("acc(xhigh, " + str(acc[0]) + ")")
278. prolog.retract("acc(xlow, " + str(acc[1]) + ")")
279. prolog.retract("acc(yhigh, " + str(acc[2]) + ")")
280. prolog.retract("acc(ylow, " + str(acc[3]) + ")")
281. prolog.retract("acc(zhigh, " + str(acc[4]) + ")")
282. prolog.retract("acc(zlow, " + str(acc[5]) + ")")
283. prolog.retract("gyro(xhigh, " + str(gyro[0]) + ")")
284. prolog.retract("gyro(xlow, " + str(gyro[1]) + ")")
285. prolog.retract("gyro(yhigh, " + str(gyro[2]) + ")")
286. prolog.retract("gyro(ylow, " + str(gyro[3]) + ")")
287. prolog.retract("gyro(zhigh, " + str(gyro[4]) + ")")
288. prolog.retract("gyro(zlow, " + str(gyro[5]) + ")")
289. prolog.retract("temp(" + str(temp) + ")")
290.
291. # angolo vecchio
292. prolog.retract("oldangle8(" + str(oldangle) + ")") 293.
294. return result
295.
296.
297. def callback(msg):
298. """

299. funzione di callback di Ros, effetua le valutazioni del mondo circostante e fa uuna scelta
300. :param msg: messaggio ros dal controller
301. :return: nulla
302. """
303. global commandolder, oldangle, commandIA, qrcode, fotocamera, switch, son ar, volt,\
304. lidar, angle8, angle16, pitch, roll, mag, acc, gyro, temp
305. qrcode = msg.qrcode
306. fotocamera = msg.visione
307. switch = msg.switches
308. switch[0] = int(switch[0])
309. switch[1] = int(switch[1])
310. switch[2] = int(switch[2])
311. sonare = msg.sonar
312. sonar = (int(sonare[0]), int(sonare[1]), int(sonare[2]))
313. volt = msg.volt
314. lidar = msg.lidar
315. angle16 = msg.angle16
316. angle8 = msg.angle8
317. pitch = msg.pitch
318. roll = msg.roll
319. mag = msg.mag
320. acc = msg.acc
321. gyro = msg.gyro
322. temp = msg.temp
323.
324.
325. def ifNotNone(qrcode, fotocamera, switch, sonar, volt, lidar, angle16, angle8 , pitch, roll, mag, acc, gyro, temp):
326. """
327. Funzione di controlo delle variabili globali,
328. controlla se sono state modificate tutte
329. :param qrcode:
330. :param fotocamera:
331. :param switch:
332. :param sonar:
333. :param volt:
334. :param lidar:
335. :param angle16:
336. :param angle8:
337. :param pitch:
338. :param roll:
339. :param mag:
340. :param acc:
341. :param gyro:
342. :param temp:
343. :return: True se non sono None e False se sono None
344. """
345. return qrcode is not None and fotocamera is not None and switch is not No ne and sonar is not None and\
346. volt is not None and lidar is not None and angle16 is not None and angle8 is not None and\
347. pitch is not None and roll is not None and mag is not None and acc is not None and\
348. gyro is not None and temp is not None
349.
350.
351. def main():
352. global commandolder, oldangle, commandIA, qrcode, fotocamera, switch, son ar,\
353. volt, lidar, angle8, angle16, pitch, roll, mag, acc, gyro, temp, lida rm
354. commandIA = ''
355. prologinit_and_rules()
356. print("prolog rules")

357. rospy.init_node("Prologo_IA_Node", disable_signals=True)
358. prolog_pub = rospy.Publisher("prolog_ia", PyRobot.Prolog_IA_Node, queue_s ize=0)
359. rospy.Subscriber("controller", PyRobot.Controller_Node, callback)
360. r = rospy.Rate(1)
361. while not rospy.is_shutdown():
362. if commandIA == '':
363. if ifNotNone(qrcode, fotocamera, switch, sonar, volt, lidar,
364. angle16, angle8, pitch, roll, mag, acc, gyro, temp):

365.
366. if commandolder == "correggi_a_destra" or\
367. commandolder == "correggi_a_sinistra" or oldangle is None:
368. oldangle = angle8
369.
370. commandIA = prologIA(commandolder, qrcode, fotocamera, switch , sonar, volt, lidar,
371. angle16, angle8, pitch, roll, mag, acc, gyro, temp, oldangle, lidarm)
372.
373. if commandIA == "sinistra" or commandIA == "destra" or comman dIA == "indietro":
374. oldangle = None
375.
376. commandolder = None
377. commandolder = commandIA[0]['Result']
378. prolog_msg.risposta = commandIA[0]['Result']
379. prolog_pub.publish(prolog_msg)
380. rospy.loginfo(prolog_msg)
381. commandIA = ''
382. resetNone()
383. r.sleep()
384.
385.
386. if __name__ == '__main__':
387. try:
388. main()
389. except rospy.ROSInterruptException:
390. pass

NODE LAUNCHER

Programma di avvio dei Nodi

1. <launch>
2. <node pkg="py_robot" type="Prolog_IA_Node.py" name="Prolog_IA_Node" output="scre en">
3. </node>
4. <node pkg="py_robot" type="Opencv_Node.py" name="Opencv_Node" output="screen">
5. </node>
6. </launch>

MESSAGGI

COMPASS NODE MESSAGE

1. int16 angle16
2. int8 angle8
3. int16 pitch
4. int16 roll
5. int16[6] mag
6. int16[6] acc
7. int16[6] gyro
8. int16 temp

CONTROLLER NODE MESSAGE

1. int8 qrcode
2. string fotocamera
3. bool[3] switches
4. float64[3] sonar
5. float32 volt
6. int16 angle16
7. int8 angle8
8. int16 pitch
9. int16 roll
10. int16[6] mag
11. int16[6] acc
12. int16[6] gyro
13. int16 temp
14. string visione

CONTROLLER TO MOTOR NODE MESSAGE

1. string velo

MV CAMERA NODE MESSAGE

1. string eureca

MOTOR_SWITCH NODE MESSAGE

1. bool[3] switches

PI CAMERA NODE MESSAGE

1. string visione

PROLOG IA NODE MESSAGE

1. string risposta

SONAR_VOLT NODE MESSAGE

1. float64[3] sonar
2. float32 volt

# CODICI VREP

NODI

CONTROLLER NODE

1. #! /usr/bin/python
2. import rospy
3. import py_robot.msg as PyRobot
4. import roslaunch.rlutil
5. import roslaunch.parent
6. import roslaunch
7. import time
8. import os
9.
10. controller_msg = PyRobot.Controller_Node()
11. controller_to_lidar_msg = PyRobot.Controller_To_Lidar_Node()
12. controller_to_motor_msg = PyRobot.Controller_To_Motor_Node() 13.
14. angle16 = None
15. angle8 = None
16. pitch = None
17. roll = None
18. mag = [None for x in range(0, 6)]
19. acc = [None for x in range(0, 6)]
20. gyro = [None for x in range(0, 6)]
21. temp = None
22. lidar18 = [None for x in range(0, 180)]
23. comando = None
24. switch = [None for x in range(0, 3)]
25. sonar = [None for x in range(0, 3)]
26. volt = None
27. eureca = None
28. visione = None
29. launch = None
30. risposta_prolog = None
31. fine = False
32. backflag = True
33.
34.
35. def resetvar():
36. """

37. Funzione che setta le variabili a nullo per evitare l'invio di messaggi non comp leti.
38. Lavora sulle variabili globali angle16, angle8, pitch, roll, mag, acc, gyro,
39. temp, lidar18, comando, switch, sonar, volt, eureca e visione
40. """
41. global angle16, angle8, pitch, roll, mag, acc, gyro, temp, lidar18, switch, sona r, volt, eureca, visione, comando, risposta_prolog
42.
43. angle16 = None
44. angle8 = None
45. pitch = None
46. roll = None
47. mag = [None for x in range(0, 6)]
48. acc = [None for x in range(0, 6)]
49. gyro = [None for x in range(0, 6)]
50. temp = None
51. lidar18 = [None for x in range(0, 180)]
52. comando = None
53. switch = [None for x in range(0, 3)]
54. sonar = [None for x in range(0, 3)]
55. volt = None
56. eureca = None
57. visione = None
58. risposta_prolog = None 59.
60.
61. def callback_prolog(msg):
62. """
63. funzione di callback per i messaggi provenienti dal nodo Prolog_IA,
64. modifica la variabile globale comando
65. :param msg: messagio ricevuto
66. :return: nulla
67. """
68. global comando, fine, risposta_prolog
69. comando = ""
70. risposta_prolog = msg.risposta
71. print("prolog")
72. if risposta_prolog == 'avanti':
73. comando = "e"
74. elif risposta_prolog == 'destra':
75. comando = "r"
76. elif risposta_prolog == 'sinistra':
77. comando = "q"
78. elif risposta_prolog == 'indietro':
79. comando = "i"
80. elif risposta_prolog == 'stop':
81. comando = "s"
82. elif risposta_prolog == 'correggi_a_destra':
83. comando = "t"
84. elif risposta_prolog == 'correggi_a_sinistra':
85. comando = "u"
86. elif risposta_prolog == 'attiva_lidar':
87. comando = "v"
88. elif risposta_prolog == 'fine':
89. comando = 's'
90. fine = True
91. else:
92. comando = 's'
93.
94.
95. def startfunction():
96. """
97. Funzione di inizio programma. Si occupa di far partire i nodi
98. :return: nulla
99. """
100. global launch

101. path = os.getcwd()
102. uuid = roslaunch.rlutil.get_or_generate_uuid(None, False)
103. roslaunch.configure_logging(uuid)
104. launch = roslaunch.parent.ROSLaunchParent(uuid, [
105. path + "/catkin_ws/src/py_robot_v_rep/launch/node_launcher.launch"]) # qui da aggiornare con il path del file launch
106. launch.start()
107. rospy.loginfo("started")
108.
109.
110. def endfunction():
111. """
112. Funzione di fine programma. Si occupa di far terminare il Nodo Controller
113. :return: nulla
114. """
115. global comando, launch
116. launch.shutdown()
117. time.sleep(1)
118. rospy.signal_shutdown('Mission Complete') 119.
120.
121. def callback_switch(msg):
122. """
123. Funzione Callback che processa i dati inviati dai Nodo Motor_Switch
124. :param msg: messaggio ROS dal Nodo Motor_Switch
125. """
126. global switch
127. switch = msg.switches
128. print("switch")
129.
130.
131. def callback_sonar_volt(msg):
132. """
133. Funzione Callback che processa i dati inviati dai Nodo Sonar_Volt
134. :param msg: messaggio ROS dal Nodo Sonar_Volt
135. """
136. global sonar, volt
137. sonar = msg.sonar
138. volt = msg.volt
139. print("sonar_volt")
140.
141.
142. def callback_lidar_compass(msg):
143. """
144. Funzione Callback che processa i dati inviati dai Nodo Lidar_Compass
145. :param msg: messaggio ROS dal Nodo Lidar_Compass
146. """
147. global angle16, angle8, pitch, roll, mag, acc, gyro, temp, lidar18
148. lidar18 = msg.lidar
149. angle16 = msg.angle16
150. angle8 = msg.angle8
151. pitch = msg.pitch
152. roll = msg.roll
153. mag = msg.mag
154. acc = msg.acc
155. gyro = msg.gyro
156. temp = msg.temp
157. print("lidar_compass") 158.
159.
160. def callback_mvcamera(msg):
161. """
162. Funzione Callback che processa i dati inviati dai Nodo MV_Camera
163. :param msg: messaggio ROS dal Nodo MV_Camera
164. """

165. global eureca
166. eureca = msg.eureca
167. print("mv_camera")
168.
169.
170. def callback_pi_camera(msg):
171. """
172. Funzione Callback che processa i dati inviati dai Nodo PI_Camera
173. :param msg: messaggio ROS dal Nodo PI_Camera
174. """
175. global visione
176. visione = msg.visione
177. print ("pi_camera")
178.
179.
180. def ifNotNone(angle16, angle8, pitch, roll, mag, acc, gyro, temp, volt, sonar , visione):
181. """
182. funzione di controlo delle variabili globali,
183. controlla se sono state modificate tutte
184. :param risposta_prolog:
185. :param visione:
186. :param angle16: misura del angolo a 16
187. :param angle8: misura del angolo a 8
188. :param pitch: misura del pitch
189. :param roll: misura del roll
190. :param mag: misura del mag
191. :param acc: misura del acc
192. :param gyro: misura del gyro
193. :param temp: misura della temperatura
194. :param comando: variabile del comando da inviare
195. :param volt: misura della batteria
196. :param sonar: misura dei sonar
197. :return: True se sono modificate, False se sono ancora None
198. """
199. return angle16 is not None and angle8 is not None and pitch is not None a nd roll is not None and mag is not None and acc is not None and gyro is not None and temp is not None and volt is not None and sonar is not None and visione is not None

200.
201.
202. def main():
203. """
204. Funzione principale che si occupa di inizializzare il Nodo, i Pubblisher e i Subscriber. Si occupa anche di salvare
205. i valori ricevuti dai vari Nodi nei mesaggi Controller_Node.msg e Control ler_To_Lidar.msg.
206. """
207. global angle16, angle8, pitch, roll, mag, acc, gyro, temp, lidar18, switc h, sonar, volt, eureca, visione, comando
208. global fine, risposta_prolog, backflag
209. resetvar()
210. # inizializzazione nodo Controller
211. rospy.init_node("Controller_Node", disable_signals=True)
212. startfunction()
213. # inizializzazioni Publisher e Subsciber
214. controller_pub = rospy.Publisher("controller", PyRobot.Controller_Node, q ueue_size=1)
215. controller_to_lidar_pub = rospy.Publisher("controller_To_Lidar", PyRobot. Controller_To_Lidar_Node, queue_size=1)
216. controller_to_motor_pub = rospy.Publisher("controller_To_Motor", PyRobot. Controller_To_Motor_Node, queue_size=1)
217. rospy.Subscriber("prolog_ia", PyRobot.Prolog_IA_Node, callback_prolog)
218. rospy.Subscriber("switches", PyRobot.Motor_Switch_Node, callback_switch)

219. rospy.Subscriber("sonar_volt", PyRobot.Sonar_Volt_Node, callback_sonar_vo lt)
220. rospy.Subscriber("mv_camera", PyRobot.MV_Camera_Node, callback_mvcamera)
221. rospy.Subscriber("lidar_compass", PyRobot.Lidar_Compass_Node, callback_li dar_compass)
222. rospy.Subscriber("pi_camera", PyRobot.Pi_Camera_Node, callback_pi_camera)
223. r = rospy.Rate(0.5)
224. while not rospy.is_shutdown():
225. if ifNotNone(angle16, angle8, pitch, roll, mag, acc, gyro, temp, volt , sonar, visione):
226. print (switch)
227. controller_msg.lidar = lidar18 # messaggio per il nodo Prolog pe r distanze lidar
228. controller_msg.angle16 = angle16 # messaggio per il nodo Prolog per angle16
229. controller_msg.angle8 = angle8 # messaggio per il nodo Prolog pe r angle8
230. controller_msg.pitch = pitch # messaggio per il nodo Prolog per pitch
231. controller_msg.roll = roll # messaggio per il nodo Prolog per ro ll
232. controller_msg.mag = mag # messaggio per il nodo Prolog per mag
233. controller_msg.acc = acc # messaggio per il nodo Prolog per acc
234. controller_msg.gyro = gyro # messaggio per il nodo Prolog per gy ro
235. controller_msg.temp = temp # messaggio per il nodo Prolog per te mp
236. controller_msg.switches = switch # messaggio per il nodo Prolog per switch
237. controller_msg.volt = volt # messaggio per il nodo Prolog per vo lt
238. controller_msg.sonar = sonar # messaggio per il nodo Prolog per sonar
239. controller_msg.visione = visione # messaggio per il nodo Prolog per Py Camera
240.
241. if eureca == 'trovato':
242. controller_msg.qrcode = 1 # messaggio per il nodo Prolog per qrcode
243.
244. if risposta_prolog != 'attiva_lidar':
245. controller_to_lidar_msg.on_off_lidar = False
246. backflag = True
247.
248. if risposta_prolog == 'attiva_lidar' and backflag: # messaggio p er il Nodo Compass_Servo_Lidar
249. controller_to_lidar_msg.on_off_lidar = True
250. backflag = False
251.
252. if comando is not None:
253. controller_to_motor_msg.velo = comando # messaggio per il no do Motor_Switch per Motor
254.
255. # funzioni Publish ROS
256. controller_pub.publish(controller_msg)
257. controller_to_lidar_pub.publish(controller_to_lidar_msg)
258. controller_to_motor_pub.publish(controller_to_motor_msg)
259. rospy.loginfo(controller_msg)
260. rospy.loginfo(controller_to_lidar_msg)
261. rospy.loginfo(controller_to_motor_msg)
262. if fine:
263. time.sleep(2)

264. endfunction()
265. resetvar()
266. r.sleep()
267.
268.
269. if __name__ == '__main__':
270. try:
271. main()
272. except rospy.ROSInterruptException:
273. pass

LIDAR_COMPASS NODE

1. #! /usr/bin/python
2.
3. from librerie import *
4. import numpy as np
5. import time
6. import rospy
7. import py_robot_v_rep.msg as PyRobot
8.
9. oggetto = []
10. lidar_compass_msg = PyRobot.Lidar_Compass_Node()
11. lidarvar = [0.] * 18
12. clientID = None
13. handle = None
14. flagtrue = False
15.
16.
17. def connessione():
18. """
19. funzione per connessione
20. :return: clientID
21. """
22. print('Program started')
23. simxFinish(-1) # just in case, close all opened connections
24. clientID = simxStart('127.0.0.1', 19998, True, True, 5000, 5) # Connect to V-REP
25. if clientID == -1:
26. print("Failed to connect to Remote API Server")
27. else:
28. print('Connected to Remote API Server')
29. return clientID
30.
31.
32. def oggetti(clientID):
33. """
34. funzione che crea l'oggetto lidar nel modo v-rep
35. :var globale oggetto: rappresenta l'oggetto lidar, e' di tipo lista
36. :param clientID: connesione v-rep
37. :return: oggetto
38. """
39. global oggetto
40. nomioggetti = ['Lidar']

41. res, objecthandle = simxGetObjectHandle(clientID, nomioggetti[0], simx_opmode_bl ocking)
42. simxReadProximitySensor(clientID, objecthandle, simx_opmode_streaming)
43. simxGetObjectOrientation(clientID, objecthandle, sim_handle_parent, simx_opmode_ streaming)
44. if not res == 0:
45. print ("Creation Error")
46. return
47. else:
48. print ("Creation " + nomioggetti[0])
49. oggetto.append(objecthandle)
50. return oggetto
51.
52.
53. def readproximity(clientID, handle):
54. """
55. funzione che ritorna una lettura, la lettura in questo caso e' del lidar
56. :param clientID: connessione v-rep
57. :param handle: oggetto dal quale provine la lettura
58. :return ditsanza: distanza letta
59. """
60. ris, stato, coordinate, handleoggettoris, vettorenormalizzato = simxReadProximit ySensor(clientID, handle,
61.
simx_opmode_buffer)
62. if ris > 0:
63. print ("Error read proximity")
64. distanza = np.linalg.norm(coordinate)
65. return distanza
66.
67.
68. def angololidar(clientID, lidarhandle):
69. """
70. funzione che ci dice l' orientamento del oggetto passato rispetto al padre nel m ondo v-rep,
71. in quessto caso e' l'orientamento del lidar rispetto il padre (corpo del rover)
72. :param clientID: connessione v-rep
73. :param handle: oggetto a qui misurare l' orientamento rispetto al padre
74. :return number: lista che contiene la rotazione rispetto ai 3 assi (misura in gr adi deg)
75. """
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

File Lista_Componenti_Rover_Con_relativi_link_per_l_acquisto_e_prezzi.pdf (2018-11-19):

# Lista Componenti Rover Con relativi link per l'acquisto e prezzi

## Questa variante prevede la stampa in 3D del telaio del rover

| Nome | Link per l'acquisto | Note | Quantità | Prezzo unitario | Spese di spedizione
1 | Motore Dc12v 100rpm | www.banggood.com (https://www.banggood.com/it/DC12V-100RPM-Powerful-High-Torque-Gear-Box-Motor-Speed-Reduction-p-941184.html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) | | 4 | € 7,22 | € 0,00
2 | 2x Ruota Rover 120x60mm con adattatori per alberi | www.melopero.com (https://www.melopero.com/shop/robotica/dagu-wild-thumper-wheel-120x60mm-pair-with-4mm-shaft-adapters-chrome/) | | 2 | € 16,26 | € 6,98
3 DC Stepper Motor Driver Module | Controller L298N | www.amazon.it (https://www.amazon.it/L298N-Bridge-Stepper-Controller-Arduino/dp/B013QTC18K) | | 1 | € 3,50 | € 0,00
4 Multistar Hight Capacity | 5200mAh 3S | www.hobbyking.com (https://hobbyking.com/it_it/multistar-high-capacity-5200mah-3s-12c-multi-rotor-lipo-pack-w-xt60.html) | | 1 | € 22,32 | € 0,00
5 | XT60 Panel Mounting Kit | www.hobbyking.com (https://hobbyking.com/en_us/xt60-panel-mounting-kit.html?wrh_pdp=7) | | 1 | € 2,32
6 Turnigy Accucel-6 80W 10A | Balancer Charger LiHV | www.hobbyking.com (https://hobbyking.com/it_it/turnigy-accucel-6-80w-10a-balancer-charger-lihv-capable.html) | A fine lista ci saranno i totali con e senza caricatore e sensore di temperatura | 1 | € 30,51
7 Turnigy sensore di temperatura | per il caricabatteria | www.hobbyking.com (https://hobbyking.com/it_it/multistar-high-capacity-5200mah-3s-12c-multi-rotor-lipo-pack-w-xt60.html) | | 1 | € 2,89
8 Turnigy® ignifugo LiPoly Bag | Batteria | www.hobbyking.com (https://hobbyking.com/it_it/fire-retardant-lipo-battery-bag-220x155x115mm-with-handle.html) | | 1 | € 3,67
9 Set 2 Lipo Voltage Checker (2S - | 8S) | www.amazon.it (https://www.amazon.it/WOSKY-Battery-Indicator-helicopter-quadcopter/dp/B072J71G72) | | 1 | € 7,99 | € 0,00
10 | Vetro Sintetico Trasparente in Lastra Maurer 500x250 mm spessore 4 mm | www.amazon.it (https://www.amazon.it/Sintetico-Trasparente-Lastra-500x250-spessore/dp/B00HWRE7SK/) | | 1 | € 7,90 | € 0,00
11 | Cavo XT60 400mm | www.banggood.com (https://www.banggood.com/it/400mm-XT60-Female-Plug-To-XT60-Male-Plug-Adapter-Connector-p-1137564.html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) | | 2 | € 1,79 | € 0,00
12 | Set 5 interruttori 16A 250V | www.amazon.it (https://www.amazon.it/gp/product/B00WJLF8OQ/) | Per questo progetto ne occorrono solamente 2, i restanti potranno essere utilizzati per altri rover | 1 | € 6,99 | € 0,00
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

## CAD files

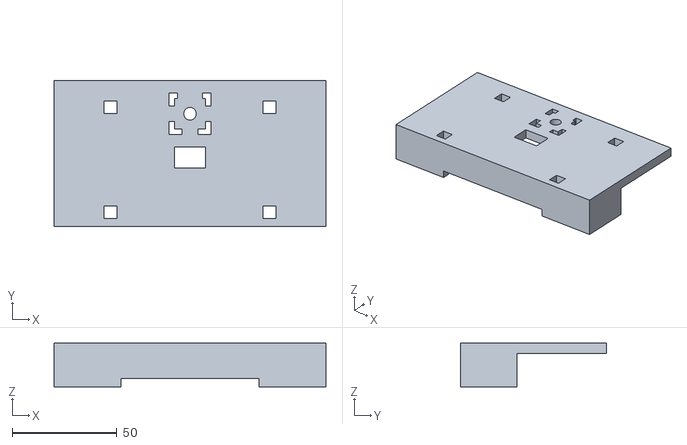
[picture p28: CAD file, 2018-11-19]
3D Elements/Modelli ftl 3D dei componenti da stampare/Coperchio.stl
130.0 x 70.0 x 21.0

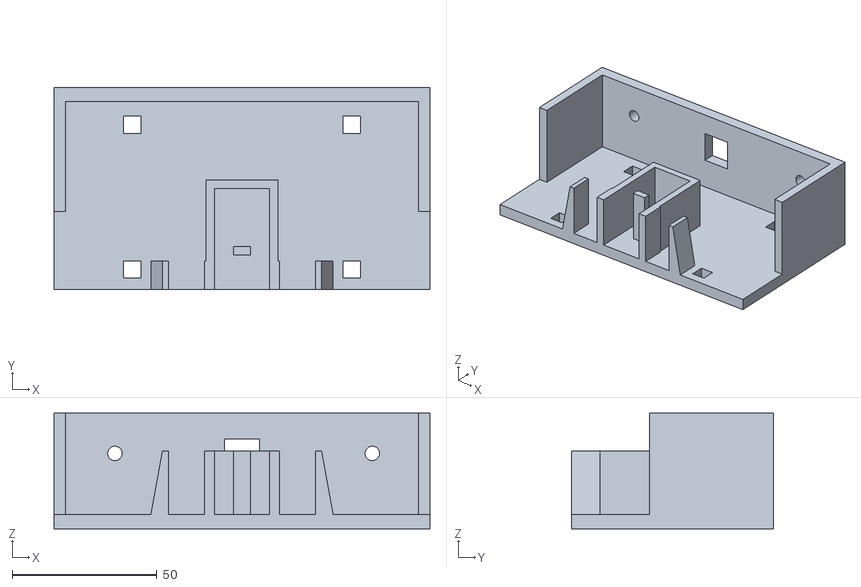
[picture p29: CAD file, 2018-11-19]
3D Elements/Modelli ftl 3D dei componenti da stampare/Corpo Principale.stl
130.0 x 70.0 x 40.0

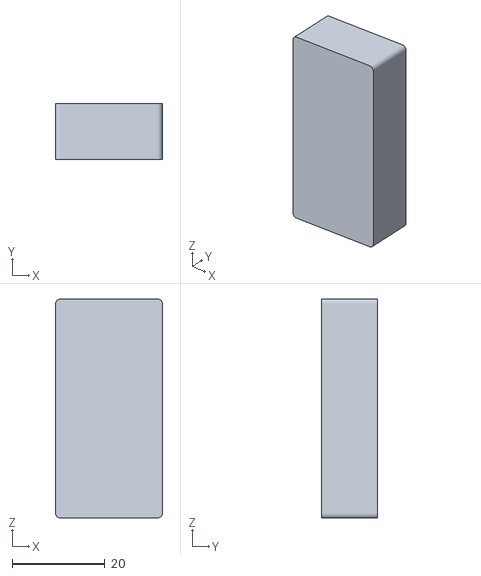
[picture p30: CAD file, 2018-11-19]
3D Elements/Modelli ftl 3D dei componenti da stampare/Case Arduino tipo 1.stl
23.0 x 12.0 x 47.2

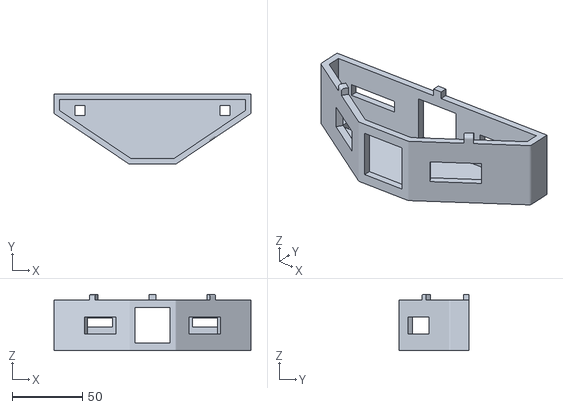
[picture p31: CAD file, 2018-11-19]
3D Elements/Modelli ftl 3D dei componenti da stampare/Scatola Posteriore.stl
140.0 x 50.0 x 40.0

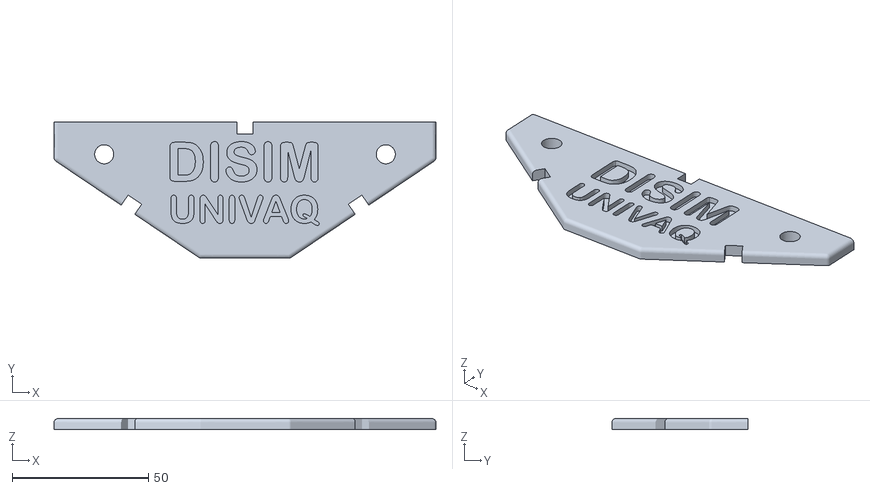
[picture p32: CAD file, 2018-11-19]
3D Elements/Modelli ftl 3D dei componenti da stampare/Coperchio scatola posteriore.stl
140.0 x 50.0 x 4.00

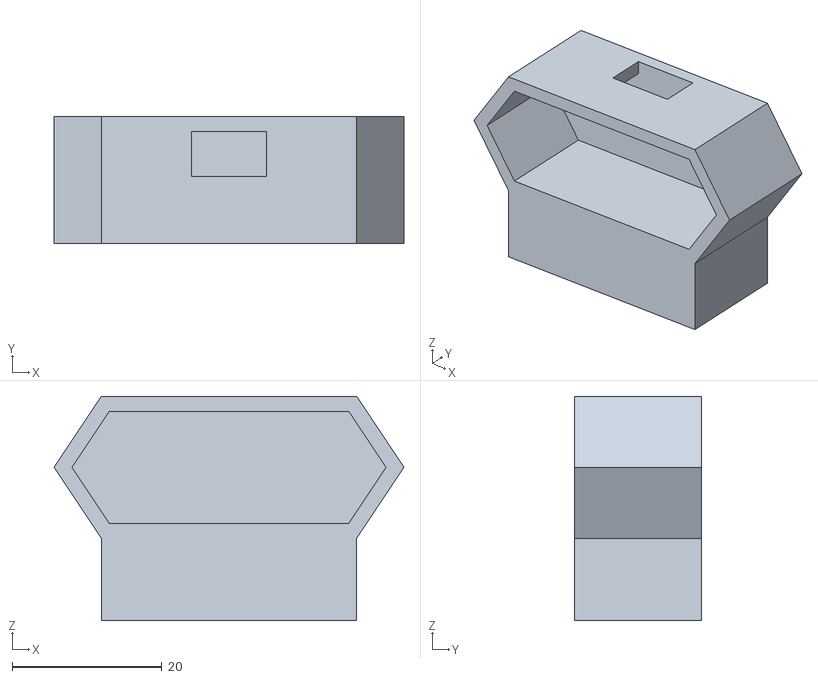
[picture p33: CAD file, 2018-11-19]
3D Elements/Modelli ftl 3D dei componenti da stampare/Case Lidar.stl
46.8 x 17.0 x 30.0

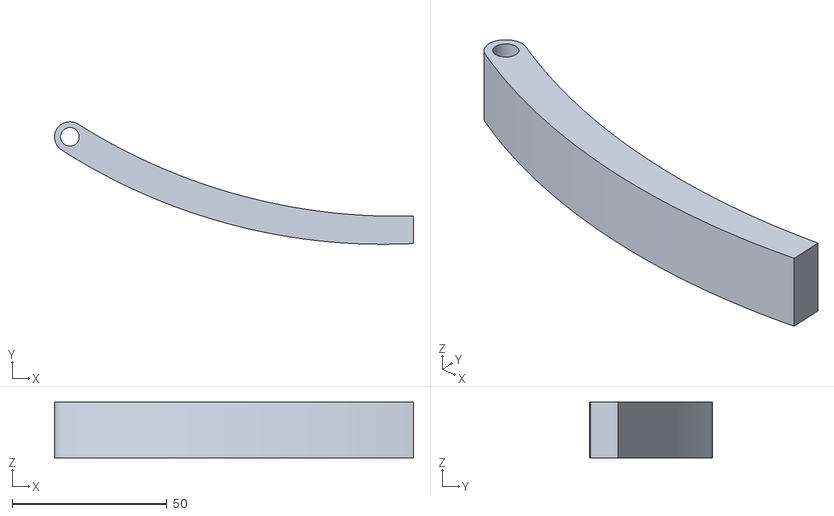
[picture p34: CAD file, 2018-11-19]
3D Elements/Modelli ftl 3D dei componenti da stampare/Aletta Sinistra.stl
115.8 x 39.6 x 18.0

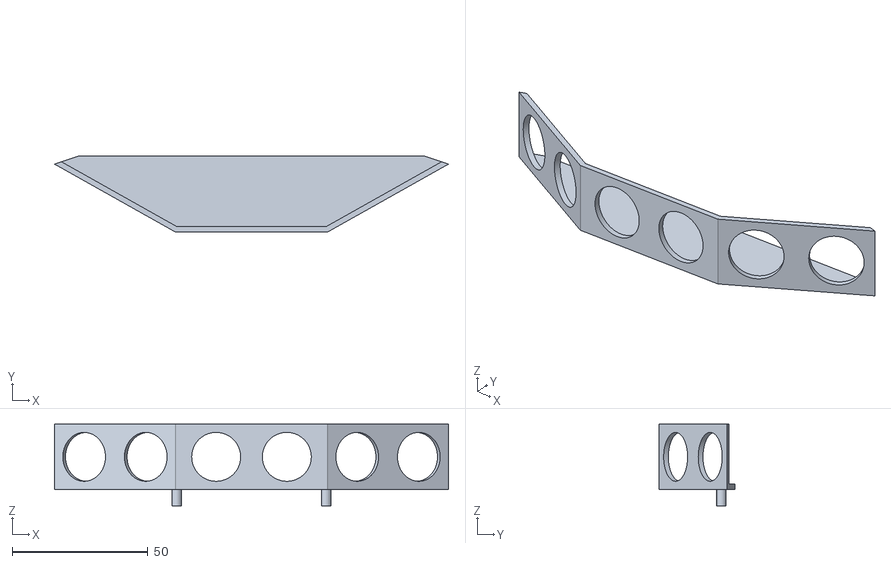
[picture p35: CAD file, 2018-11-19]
3D Elements/Modelli ftl 3D dei componenti da stampare/Supporto Sonar.stl
145.0 x 28.0 x 30.0

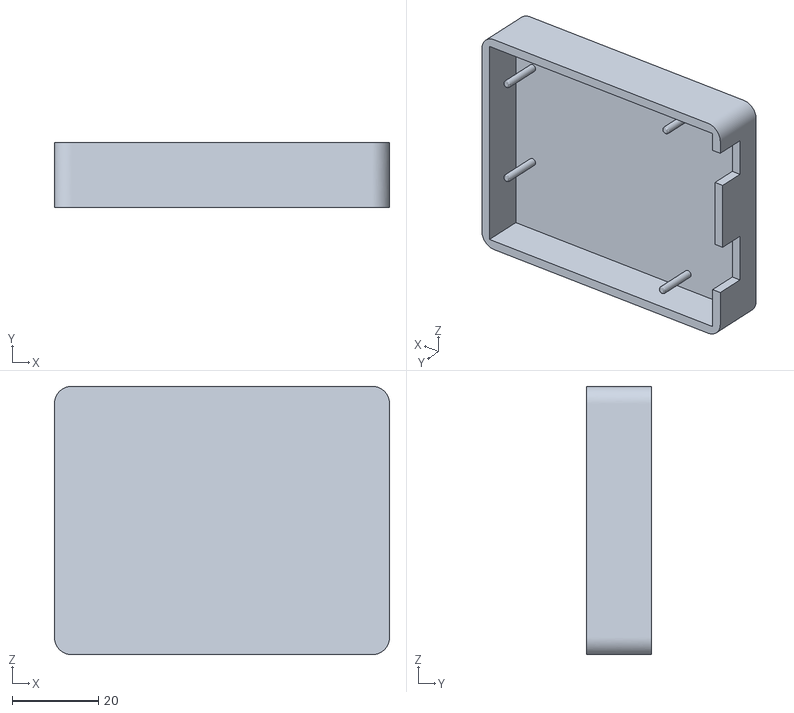
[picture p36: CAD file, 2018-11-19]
3D Elements/Modelli ftl 3D dei componenti da stampare/Case Arduino.stl
77.9 x 15.0 x 62.4

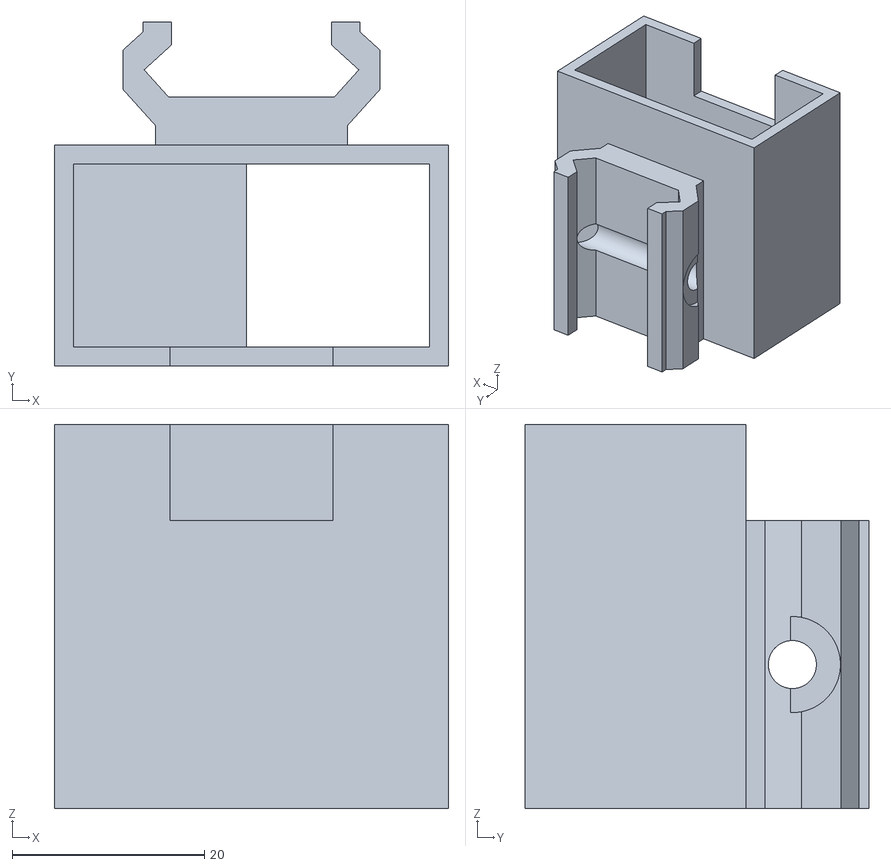
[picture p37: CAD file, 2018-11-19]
3D Elements/Modelli ftl 3D dei componenti da stampare/Carrello OpenMV.stl
41.0 x 35.8 x 40.0

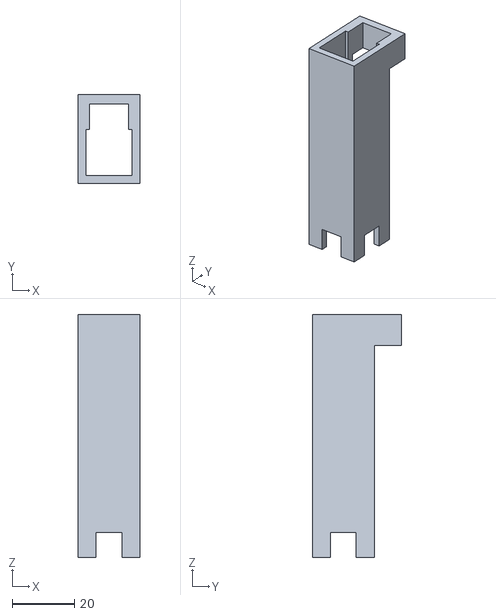
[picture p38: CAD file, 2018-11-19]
3D Elements/Modelli ftl 3D dei componenti da stampare/Torre.stl
19.8 x 28.5 x 78.0

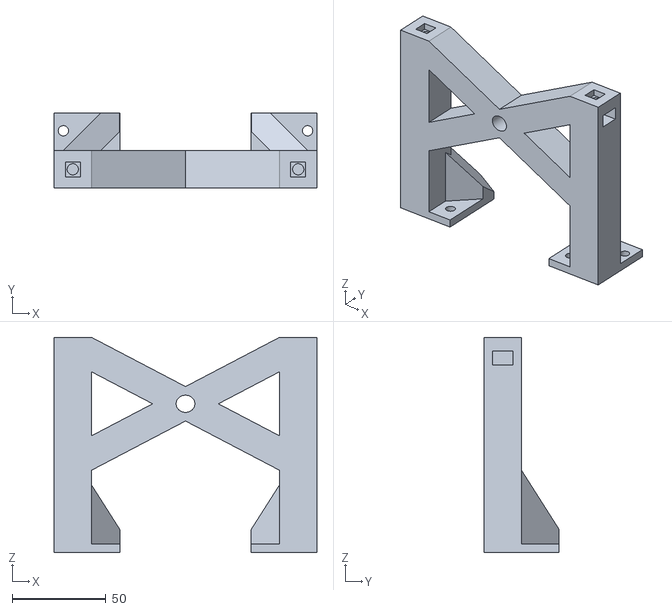
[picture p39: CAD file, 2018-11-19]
3D Elements/Modelli ftl 3D dei componenti da stampare/X Anteriore.stl
140.0 x 40.0 x 114.6

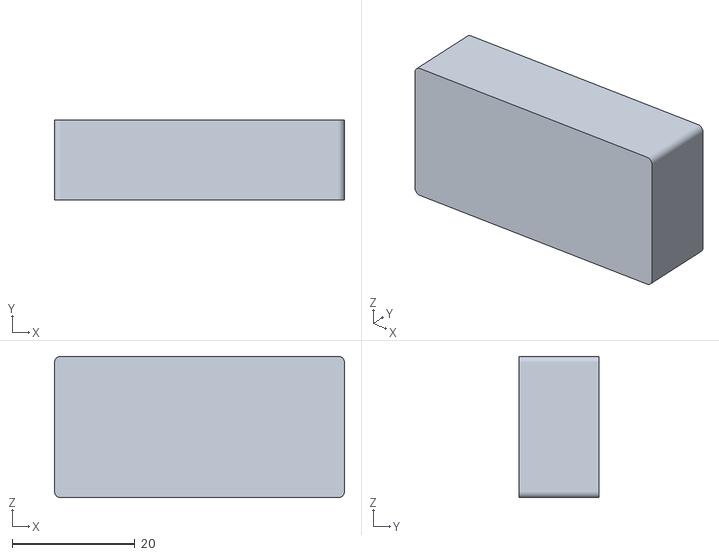
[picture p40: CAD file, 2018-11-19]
3D Elements/Modelli ftl 3D dei componenti da stampare/Case arduino tipo 2.stl
47.2 x 13.0 x 23.0

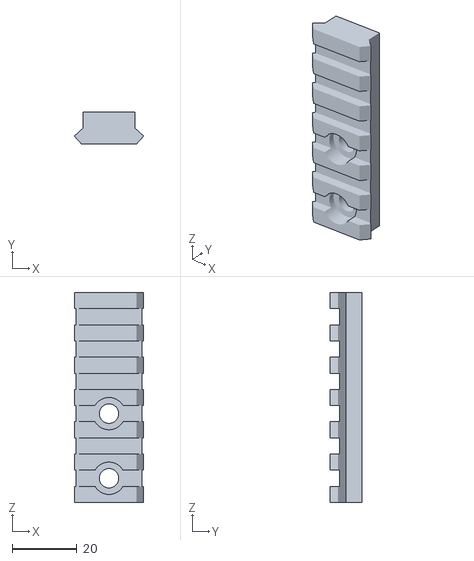
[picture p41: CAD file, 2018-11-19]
3D Elements/Modelli ftl 3D dei componenti da stampare/Slitta Torre.stl
21.5 x 10.0 x 65.0

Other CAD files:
3D Elements/Modelli ftl 3D dei componenti da stampare/Aletta_Destra.stl
3D Elements/Modelli ftl 3D dei componenti da stampare/Corpo Frontale.stl
3D Elements/Modelli ftl 3D dei componenti da stampare/Supporto Batteria.stl

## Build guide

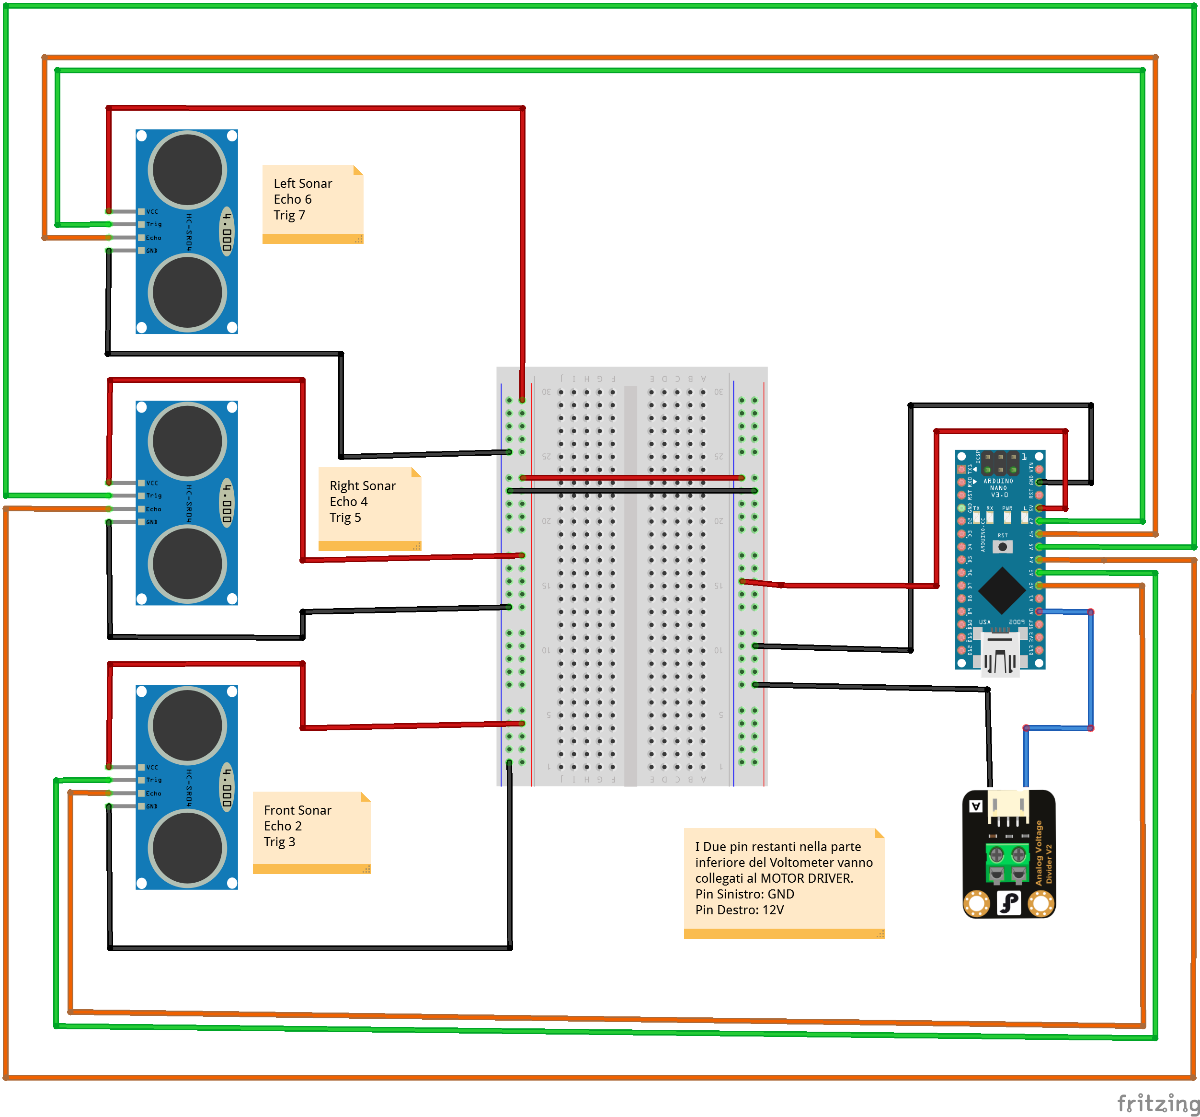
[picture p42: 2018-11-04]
py_robot/other/Arduino Nodes/Wiring diagrams/Imgs Wiring Diagrams/Sonar_e_volt.png

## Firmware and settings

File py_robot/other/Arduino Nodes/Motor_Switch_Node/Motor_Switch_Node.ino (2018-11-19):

// libreria ros
#include <ros.h>
// custom message Motor_Switch_Node
#include <py_robot/Motor_Switch_Node.h>
// custom message Controller_Node
#include <py_robot/Controller_To_Motor_Node.h>

// handle nodon ROS
ros::NodeHandle nh;

// assegnamento pin motori 1 e 2
#define SXPWM 3
#define SXIN1 4
#define SXIN2 5

// assegnamento pin motori 3 e 4
#define DXPWM 6
#define DXIN1 7
#define DXIN2 8


// assegnamento pin switch
#define switchFront 11
#define switchLeft 10
#define switchRight 9

// variabili globali
String comando;
int vel;

//funzione callback
// PARAM: messaggio ros velo

void callback( const py_robot::Controller_To_Motor_Node& velo) {
  // assegnamento del comando impartito dal Nodo Controller
  comando = velo.velo;

}
// funzione sottoscrizione di ros
ros::Subscriber<py_robot::Controller_To_Motor_Node> motor_sub("controller_To_Motor", callback);

// ros custom message sonar_volt
py_robot::Motor_Switch_Node switches;

// ros inizializzazione Pubblisher sonar_volt
ros::Publisher switch_pub("switches", &switches);

// funzione per switch
// PARAM: switchpin
// RETURN 0 se il lo switch non è attivato, 1 se è attivato

void setup() {
  // inizializzazione nodo
  nh.initNode();
  nh.advertise(switch_pub);
  nh.subscribe(motor_sub);

  // pin switch
  pinMode(switchFront, INPUT);
  pinMode(switchRight, INPUT);
  pinMode(switchLeft, INPUT);
  // pin motori 1 e 2 di sinistra
  pinMode(SXPWM, OUTPUT);
  pinMode(SXIN1, OUTPUT);
  pinMode(SXIN2, OUTPUT);
  analogWrite(SXPWM, 0);

  // pin motori 3 e 4 di destra
  pinMode(DXPWM, OUTPUT);
  pinMode(DXIN1, OUTPUT);
  pinMode(DXIN2, OUTPUT);
  analogWrite(DXPWM, 0);

  delay(1000);
}

// funzione per switch
// PARAM: switchpin
// RETURN 0 se il lo switch non è attivato, 1 se è attivato

long switchsensor(int switchpin) {
  // controllo se lo switch è stato premuto
  if (digitalRead(switchpin) == HIGH) {
    delay(20);
    // dopo 20 millisecondi controllo di nuovo se è ancora premuto per evitare errori
    if (digitalRead(switchpin) == HIGH) {
      // ritorna 0 se lo switch non è stato attivato
      return 0;
    }
  }
  // ritorna 1 se lo switch è stato attivato
  return 1;
}

// funzioni relative ai comandi da impartire ai motori

// funzione Avanti
// PARAM: intero vel: parametro velocità
// PARAM: intero tempo: parametro tempo di esecuzione
void vaiAvanti(int vel, int tempo) {
  // relativo al motor drive collegato ai motori del lato sinistro
  digitalWrite(SXIN1, 1);
  digitalWrite(SXIN2, 0);
  // velocità lato sinistro
  analogWrite(SXPWM, vel);
  // relativo al motor drive collegato ai motori del lato destro
  digitalWrite(DXIN1, 1);
  digitalWrite(DXIN2, 0);
  // velocità lato destro
  analogWrite(DXPWM, vel);

  delay(tempo);
}

// funzione Indietro
// PARAM: intero vel: parametro velocità
// PARAM: intero tempo: parametro tempo di esecuzione
void vaiIndietro(int vel, int tempo) {
  // relativo al motor drive collegato ai motori del lato sinistro
  fermo(0);
  digitalWrite(SXIN1, 0);
  digitalWrite(SXIN2, 1);
  // velocità lato sinistro
  analogWrite(SXPWM, vel);
  // relativo al motor drive collegato ai motori del lato destro
  digitalWrite(DXIN1, 0);
  digitalWrite(DXIN2, 1);
  // velocità lato destro
  analogWrite(DXPWM, vel);

  delay(tempo);
  fermo(0);
}

// funzione Sinistra
// PARAM: intero vel: parametro velocità
// PARAM: intero tempo: parametro tempo di esecuzione
void vaiDestra(int vel, int tempo) {
  // relativo al motor drive collegato ai motori del lato sinistro
  digitalWrite(SXIN1, 1);
  digitalWrite(SXIN2, 0);
  // velocità lato sinistro
  analogWrite(SXPWM, vel);
  // relativo al motor drive collegato ai motori del lato destro
  digitalWrite(DXIN1, 0);
  digitalWrite(DXIN2, 1);
  // velocità lato destro
  analogWrite(DXPWM, vel);

  delay(tempo);
  fermo(0);
  comando = "s";
}

// funzione Destra
// PARAM: intero vel: parametro velocità
// PARAM: intero tempo: parametro tempo di esecuzione
void vaiSinistra(int vel, int tempo) {
  // relativo al motor drive collegato ai motori del lato sinistro
  digitalWrite(SXIN1, 0);
  digitalWrite(SXIN2, 1);
  // velocità lato sinistro
  analogWrite(SXPWM, vel);
  // relativo al motor drive collegato ai motori del lato destro
  digitalWrite(DXIN1, 1);
  digitalWrite(DXIN2, 0);
  // velocità lato destro
  analogWrite(DXPWM, vel);

  delay(tempo);
  fermo(0);
  comando = "s";
}

// funzione Stop
// PARAM: intero vel: parametro velocità
// PARAM: intero tempo: parametro tempo di esecuzione
void fermo(int tempo) {
  // relativo al motor drive collegato ai motori del lato sinistro
  digitalWrite(SXIN1, 0);
  digitalWrite(SXIN2, 0);
  // velocità lato sinistro
  analogWrite(SXPWM, 0);
  // relativo al motor drive collegato ai motori del lato destro
  digitalWrite(DXIN1, 0);
  digitalWrite(DXIN2, 0);
  // velocità lato destro
  analogWrite(DXPWM, 0);

  delay(tempo);
}


void loop() {

  //switch case con i varin casi possibili dei comandi ricevuti dal Nodo Controller
  switch (comando[0]) {

    case 'a': vaiAvanti(100, 50);
      break;

    case 'b': vaiAvanti(150, 50);
      break;

    case 'c': vaiAvanti(200, 50);
      break;

    case 'd': vaiAvanti(255, 50);
      break;

    case 'e': vaiIndietro(150, 50);
      break;

    case 'l': vaiSinistra(255, 200);
      break;

    case 'r': vaiDestra(255, 200);
      break;

    case 'f': vaiSinistra(255, 50);   // correzione sinistra
      break;

    case 'g': vaiDestra(255, 50);    // correzione destra
      break;

    case 'h': vaiSinistra(255, 2100);  // 360 antiorario
      break;

    case 'i': vaiDestra(255, 2100);   //360 orario
      break;

    case 'm': vaiSinistra(255, 800); // 90° a sinistra
      break;

    case 'n': vaiDestra(255, 800);   // 90° a destra
      break;

    case 'o': vaiSinistra(255, 1200); // 180° a sinistra
      break;

    case 'p': vaiDestra(255, 1200);   // 180° a destra
      break;



    case 's': fermo(0);
      break;

  }

  // assegnamento valore, 0 o 1, dello switch centrale nella prima posizione dell'array switches,
  // prima variabile del custom message Motor_Switch_Node
  switches.switches[0] = switchsensor(switchFront);
  // assegnamento valore, 0 o 1, dello switch Sinistra nella seconda posizione dell'array switches,
  // prima variabile del custom message Motor_Switch_Node
  switches.switches[1] = switchsensor(switchLeft);
  // assegnamento valore, 0 o 1, dello switch Destro nella terza posizione dell'array switches,
  // prima variabile del custom message Motor_Switch_Node
  switches.switches[2] = switchsensor(switchRight);
  // funzione Publish ROS
  switch_pub.publish(&switches);
  // procedura da attuare dopo che uno degli switch viene attivato
  if (switches.switches[0] == 0 || switches.switches[1] == 0 || switches.switches[2] == 0) {
    // stop
    fermo(0);
    // indietro per ___ secondi
    vaiIndietro(150, 2000);
  }
  // attesa eventi ROS
  nh.spinOnce();
  delay(10);
}

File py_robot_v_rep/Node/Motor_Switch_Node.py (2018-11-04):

#! /usr/bin/python

from librerie import *
import numpy as np
import py_robot_v_rep.msg as PyRobot
import time
import rospy


switch_msg = PyRobot.Motor_Switch_Node()
clientID = None
oggetto = []
micros = []
motors = []
stati = []


def connessione():
    """
    funzione per connessione
    :return: clientID
    """
    print('Program started')
    simxFinish(-1)  # just in case, close all opened connections
    clientID = simxStart('127.0.0.1', 20000, True, True, 5000, 5)  # Connect to V-REP
    if clientID == -1:
        print("Failed to connect to Remote API Server at Port 20000")
    else:
        print('Connected to Remote API Server at Port 20000')
        return clientID


def oggetti(clientID):
    """
    funzione che crea gli oggetti nel modo v-rep
    :var globale oggetto: rappresenta gli oggetti creati, e' di tipo lista
    :param clientID: connesione v-rep
    :return: oggetto
    """
    global oggetto
    nomioggetti = ['Micro_SX', 'Micro_DX', 'Micro_CE', 'Motore_AD', 'Motore_AS', 'Motore_PD', 'Motore_PS']
    for i in range(0, 7):
        res, objecthandle = simxGetObjectHandle(clientID, nomioggetti[i], simx_opmode_blocking)
        if i < 4:
            simxReadProximitySensor(clientID, objecthandle, simx_opmode_streaming)
        if not res == 0:
            print ("Creation Error")
            return
        else:
            print ("Creation " + nomioggetti[i])
            oggetto.append(objecthandle)
    return oggetto


def forward(clientID, motors, velocita):
    """
    funzione che setta i motori per andare avanti
    :param clientID: connesione v-rep
    :param motors: lista degli oggetti motori del mondo v-rep
    :param velocita: velocita' da settare ai motori
    :return: nulla
    """
    ris1 = simxSetJointTargetVelocity(clientID, motors[3], velocita, simx_opmode_oneshot_wait)
    ris2 = simxSetJointTargetVelocity(clientID, motors[1], velocita, simx_opmode_oneshot_wait)
    ris3 = simxSetJointTargetVelocity(clientID, motors[2], velocita, simx_opmode_oneshot_wait)
    ris4 = simxSetJointTargetVelocity(clientID, motors[0], velocita, simx_opmode_oneshot_wait)
    if ris1 > 0 or ris2 > 0 or ris3 > 0 or ris4 > 0:
        print ("Error forward")


def backward(clientID, motors, velocita):
    """
    funzione che setta i motori per andare indietro
    :param clientID: connesione v-rep
    :param motors: lista degli oggetti motori del mondo v-rep
    :param velocita: velocita' da settare ai motori
    :return: nulla
    """
    ris1 = simxSetJointTargetVelocity(clientID, motors[3], -velocita, simx_opmode_oneshot_wait)
    ris2 = simxSetJointTargetVelocity(clientID, motors[1], -velocita, simx_opmode_oneshot_wait)
    ris3 = simxSetJointTargetVelocity(clientID, motors[2], -velocita, simx_opmode_oneshot_wait)
    ris4 = simxSetJointTargetVelocity(clientID, motors[0], -velocita, simx_opmode_oneshot_wait)
    if ris1 > 0 or ris2 > 0 or ris3 > 0 or ris4 > 0:
        print ("Error backward")


def left(clientID, motors):
    """
    funzione che setta i motori per andare a sinistra
    :param clientID: connesione v-rep
    :param motors: lista degli oggetti motori del mondo v-rep
    :return: nulla
    """
    ris1 = simxSetJointTargetVelocity(clientID, motors[0], +0.5, simx_opmode_oneshot_wait)
    ris2 = simxSetJointTargetVelocity(clientID, motors[1], -0.5, simx_opmode_oneshot_wait)
    ris3 = simxSetJointTargetVelocity(clientID, motors[2], +0.5, simx_opmode_oneshot_wait)
    ris4 = simxSetJointTargetVelocity(clientID, motors[3], -0.5, simx_opmode_oneshot_wait)
    if ris1 > 0 or ris2 > 0 or ris3 > 0 or ris4 > 0:
        print ("Error left")

def left_correction(clientID, motors):
    """
    funzione che setta i motori per eseguire una correzione a sinistra
    :param clientID: connesione v-rep
    :param motors: lista degli oggetti motori del mondo v-rep
    :return: nulla
    """
    ris1 = simxSetJointTargetVelocity(clientID, motors[0], +2, simx_opmode_oneshot_wait)
    ris2 = simxSetJointTargetVelocity(clientID, motors[1], -2, simx_opmode_oneshot_wait)
    ris3 = simxSetJointTargetVelocity(clientID, motors[2], +2, simx_opmode_oneshot_wait)
    ris4 = simxSetJointTargetVelocity(clientID, motors[3], -2, simx_opmode_oneshot_wait)
    if ris1 > 0 or ris2 > 0 or ris3 > 0 or ris4 > 0:
        print ("Error left_correction")


def right(clientID, motors):
    """
    funzione che setta i motori per andare a destra
    :param clientID: connesione v-rep
    :param motors: lista degli oggetti motori del mondo v-rep
    :return: nulla
    """
    ris1 = simxSetJointTargetVelocity(clientID, motors[0], -0.5, simx_opmode_oneshot_wait)
    ris2 = simxSetJointTargetVelocity(clientID, motors[1], +0.5, simx_opmode_oneshot_wait)
    ris3 = simxSetJointTargetVelocity(clientID, motors[2], -0.5, simx_opmode_oneshot_wait)
    ris4 = simxSetJointTargetVelocity(clientID, motors[3], +0.5, simx_opmode_oneshot_wait)
    if ris1 > 0 or ris2 > 0 or ris3 > 0 or ris4 > 0:
        print ("Error right")

def right_correction(clientID, motors):
    """
    funzione che setta i motori per eseguire una correzione a destra
    :param clientID: connesione v-rep
    :param motors: lista degli oggetti motori del mondo v-rep
    :return: nulla
    """
    ris1 = simxSetJointTargetVelocity(clientID, motors[0], -2, simx_opmode_oneshot_wait)
    ris2 = simxSetJointTargetVelocity(clientID, motors[1], +2, simx_opmode_oneshot_wait)
    ris3 = simxSetJointTargetVelocity(clientID, motors[2], -2, simx_opmode_oneshot_wait)
    ris4 = simxSetJointTargetVelocity(clientID, motors[3], +2, simx_opmode_oneshot_wait)
    if ris1 > 0 or ris2 > 0 or ris3 > 0 or ris4 > 0:
        print ("Error right_correction")

def micro(clientID):
    """
    funzione che rileva lo stato dei microswitch nel modo r-rep
    :param clientID: connesione v-rep
    :return stati: ritorna gli stati dei microswitch e' di tipo lista
    """
    global micros, stati
    for Micro in micros:
        ris, stato, coordinate, handleoggettoris, vettorenormalizzato = simxReadProximitySensor(clientID, Micro, simx_opmode_buffer)
        stati.append(stato)
    return stati
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

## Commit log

2018-09-14 sketch Sonar Switch Node Arduino Nano
2018-09-14 Ros Libraries Arduino
2018-10-08 Cartella che contiene i file .ino di Sonar_switch
2018-10-08 Bozza Sonar_switch
2018-10-09 debug motori.ino
2018-10-09 add py camera node + aggiunta nel CMake
2018-10-09 per test del nodo switch motor
2018-10-09 per test del nodo mv camera
2018-10-09 per test del nodo pi camera
2018-10-09 per test del nodo sonar volt
2018-10-11 bozza Lidar_Compass_Node V-Rep
2018-10-11 bozza Motor_Switch_Node V-Rep
2018-10-11 bozza Sonar_Volt_Node V-Rep
2018-10-12 Nodi Arduino + sketch prova arduino
2018-10-12 messaggio personalizzato con blackjack e... per il lidar + debug messaggi
2018-10-12 ammodernamento controller node + debug di altri controller
2018-10-13 piccoli debug controller node e prova motor switch node
2018-10-14 bozza Opencv_Node Py_robot (raspberry)
2018-10-18 un po di debug
2018-10-19 riaggiustamento con commenti nodi arduino
2018-10-19 remove backup.ttt (backup di vrep)
2018-10-20 Compass_Servo_Lidar Arduino uno
2018-10-22 Debug Prolog_IA_Node: invertiti i tipi di dati tra il publisher e il subscriber
2018-10-23 Debug Controller_Node V-REP: aggiornamento a ultima versione, cambiamento nome topic subscriber da switch a switches.
2018-10-23 Debug Motor_Switch_Node V-REP: aggiornamento a ultima versione, cambiamento nome topic publisher da switch a switches.
2018-10-24 Debug compass_servo_lidar ARDUINO: cambiamento nome topic publisher da lidar_compass_sub a lidar_compass, cambiamento nome topic subscriver da controller a controller_To_Lidar.
2018-10-24 Debug compass_servo_lidar Arduino: debug codice, ottimizzazione funzione loop
2018-10-24 Debug Genrale py_robot_vrep V-REP: debug codice, risoluzione problematiche varie
    [Controller_Node.py, Motor_Switch_Node.py, Opencv_Node.py]
2018-10-24 Debug Prolog_IA_Node: risolto l'errore di segmentazione, presenta un bug di tipo prolog
    [Prolog_IA_Node.py]
2018-10-24 Debug Opencv_Node V-REP: modifica valore di ritorno vai dritto in dritto
2018-10-24 Debug Lidar_Compass_Node V-REP: modifica valore iniziale delle variabili
2018-10-25 Debug compass_servo_lidar.ino Debug Motor_Switch_Node.ino
2018-10-26 Debug GENERALE su tutti i nodi v-rep piu il Prolog_IA_Node, STATO VREP FUNZIONANTE con qualche bug sulla logica prolog da rivedere
    [Controller_Node.py, Motor_Switch_Node.py, Opencv_Node.py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]
2018-10-26 Debug Controller_Node Debug Motor_Switch_Node.ino: ottimizzazione funzione in caso di impatto
2018-10-26 Debug GENERALE su tutti i nodi v-rep piu il Prolog_IA_Node STATO VREP FUNZIONANTE con qualche bug sulla logica prolog da rivedere
    [Controller_Node.py, Prolog_IA_Node.py]
2018-10-27 Debug GENERALE su tutti i nodi v-rep piu il Prolog_IA_Node STATO VREP FUNZIONANTE
2018-11-01 add Motor_Switch_Node_Lib_Riscritta add motor_driver_lib_riscritta
2018-11-01 debug Motor_Switch_Node_Lib_Riscritta
2018-11-01 debug Motor_Switch_Node_Lib_Riscritta debug motor_driver_lib_riscritta
2018-11-02 debug nodi arduino dopo il test sul rover Compass_Servo_Lidar_Node: correzione funzione compass e correzione passi servo Motor_Switch_Node: riaggiustamento pin e riggiro logica funzione motori Sonar_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
2018-11-03 commenti e riaggiustamento codice Motor_Switch_Node Sonar_Volt_Node
2018-11-04 Nodo Compass
    [Nodo_compass_.fzz]
2018-11-04 IMG Motor_Switch
2018-11-04 IMG Sonar_Voltometer
2018-11-06 ristrutturazione repository
    [Motor_Microswitch_Node.fzz, Nodo_compass_.fzz, Sonar_Switch_Node_Arduino_Nano.fzz]
2018-11-07 riadattamento simulazione nodo Motor_Switch
2018-11-07 debug e modifiche motor_switch_node
2018-11-13 Upload New File
    [Aletta_Destra.stl]
2018-11-13 3D Elements
    [Aletta Sinistra.stl, Aletta_Destra.stl, Carrello OpenMV.stl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]
2018-11-19 Nodi Periferici (ROS Distribuito) per la visione e computazione
